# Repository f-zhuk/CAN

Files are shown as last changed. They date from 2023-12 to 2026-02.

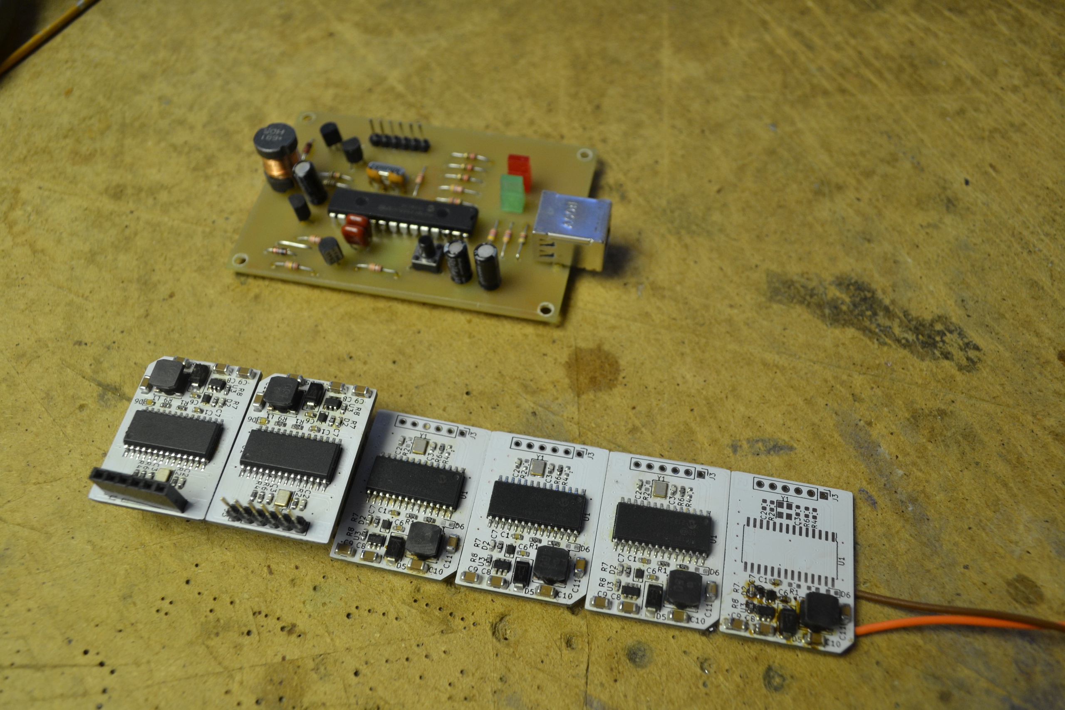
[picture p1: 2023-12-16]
CANMCU/Assemble.jpg

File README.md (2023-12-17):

# CAN
## General description
The work is in progress and is currently not ready for real-life application.  
This repository contains hardware, firmware, and software dedicated to the creation of custom CANopen systems for vehicles.  
Such custom systems could fit old cars with heavily damaged harnesses and vehicles that do not have electronic equipment by default, for example, boats, kayaks, and bicycles.
## Hardware
The complete system should consist of multiple functional blocks. Blocks should be as cheap and simple as possible while implementing complete functions like combination switch assembly, left tail light assembly, and door controls.  
Each functional block should be designed around a unified MCU module and simple interconnection boards to adapt signals from the MCU module to the systems of the block.  
Interconnection boards may provide 24LC I2C EEPROM memory for identification and non-volatile parameter storage.  
### MCU
MCU module should be self-sufficient and electrically ready for insertion in the CAN bus system. To achieve this, the MCU module has a power supply converter and CAN driver aside from the controller.  
For the first prototype, the PIC18 family was selected. PIC18F83K26 has a built-in CAN periphery and a reasonable price.  
MCU module has +12V power input, +5V power input/output, CAN, UART, 8xGPIO(PC7:PC0)  
### USB-UART
Most important interconnection board. It provides a USB to UART bridge to provide a simple debug interface.  
USB-UART board is built with MCP2200. It is connected not only through UART but also 5xGPIO. Additionally, 24LC16 I2C EEPROM memory is connected to C6 and C7. C5 is connected to the bus termination control.  
## Firmware
Heavily updated code described in AN945. The application note code was written for an older MCU. PIC18F83K26AN945 is not supported by the compiler the code was written for and the code is not compatible with the new compiler.  
AN945 default config:  
ADC is on (probably unused)  
PORT D is all output (probably unused)  
PORT B pin 5 is bit 0 of TPDO1, pin 4 is bit 1  
State of PORTB pins 4 and 5 compared to their states on previous DemoProcessEvents() call, change, rise and fall events detected and distinguished, written to OD  
Dictionary object 0x6005subondex 1 (uIOinIntEnable) bits 0 and 1  
Async transmission for TPDO1 by default  
PDO transmission type could be changed by writing to TPDO1 subindex 2  
## Software
The software is written in Python.

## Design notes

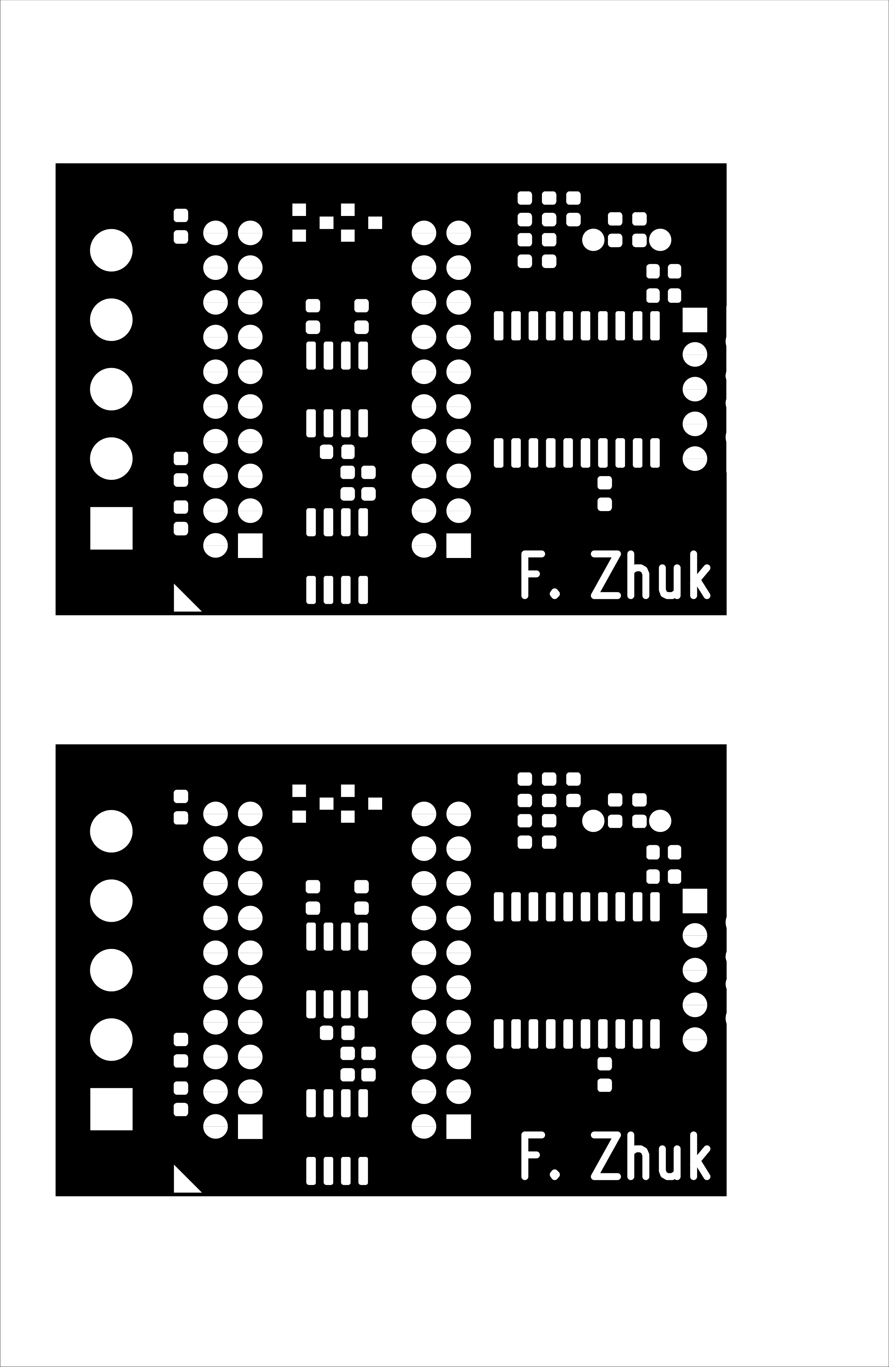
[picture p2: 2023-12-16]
USB-UART/B_Mask.png

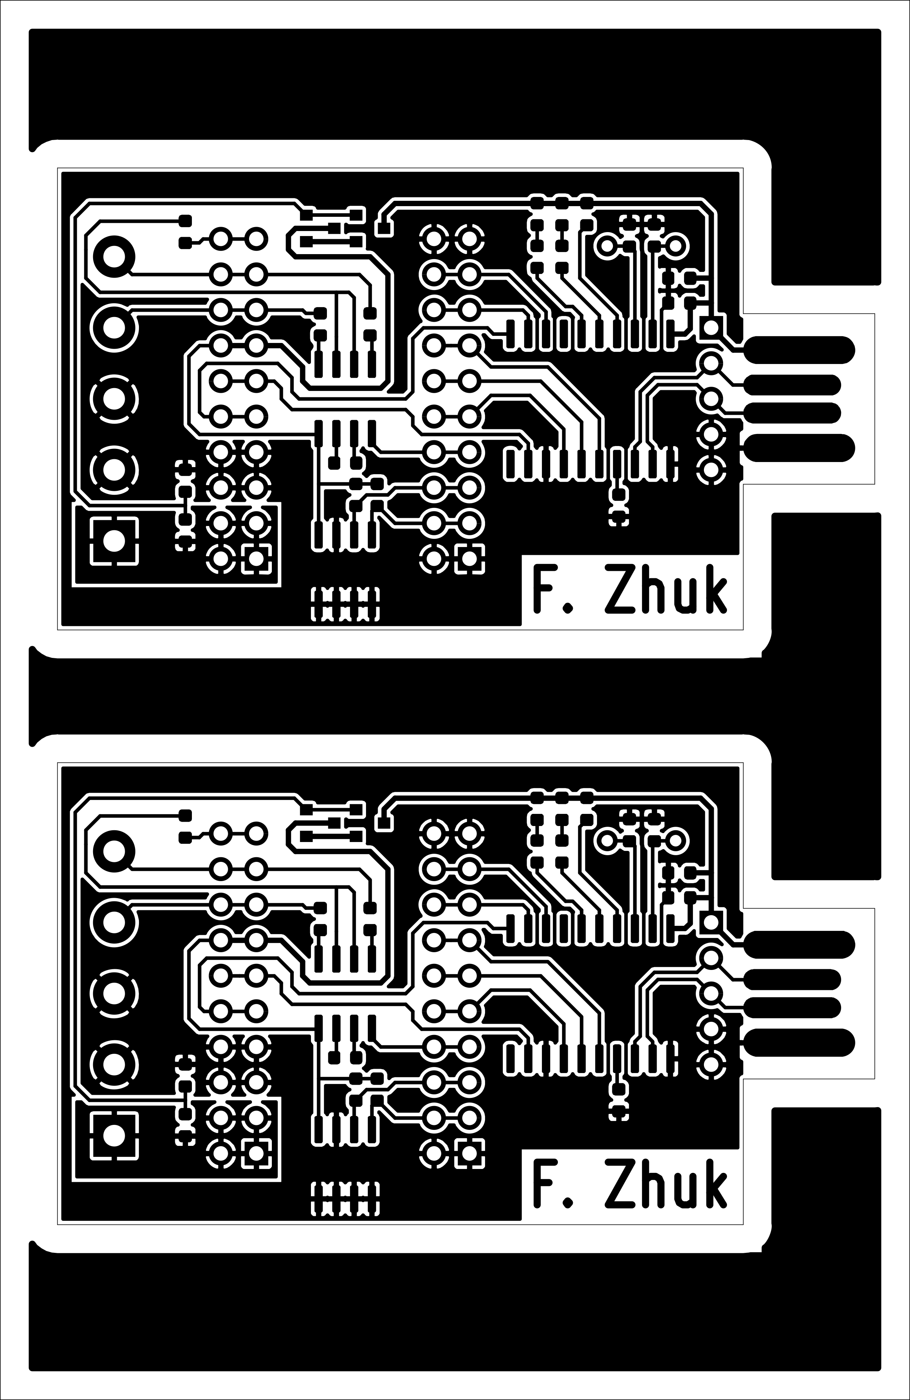
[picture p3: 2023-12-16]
USB-UART/B_Cu.png

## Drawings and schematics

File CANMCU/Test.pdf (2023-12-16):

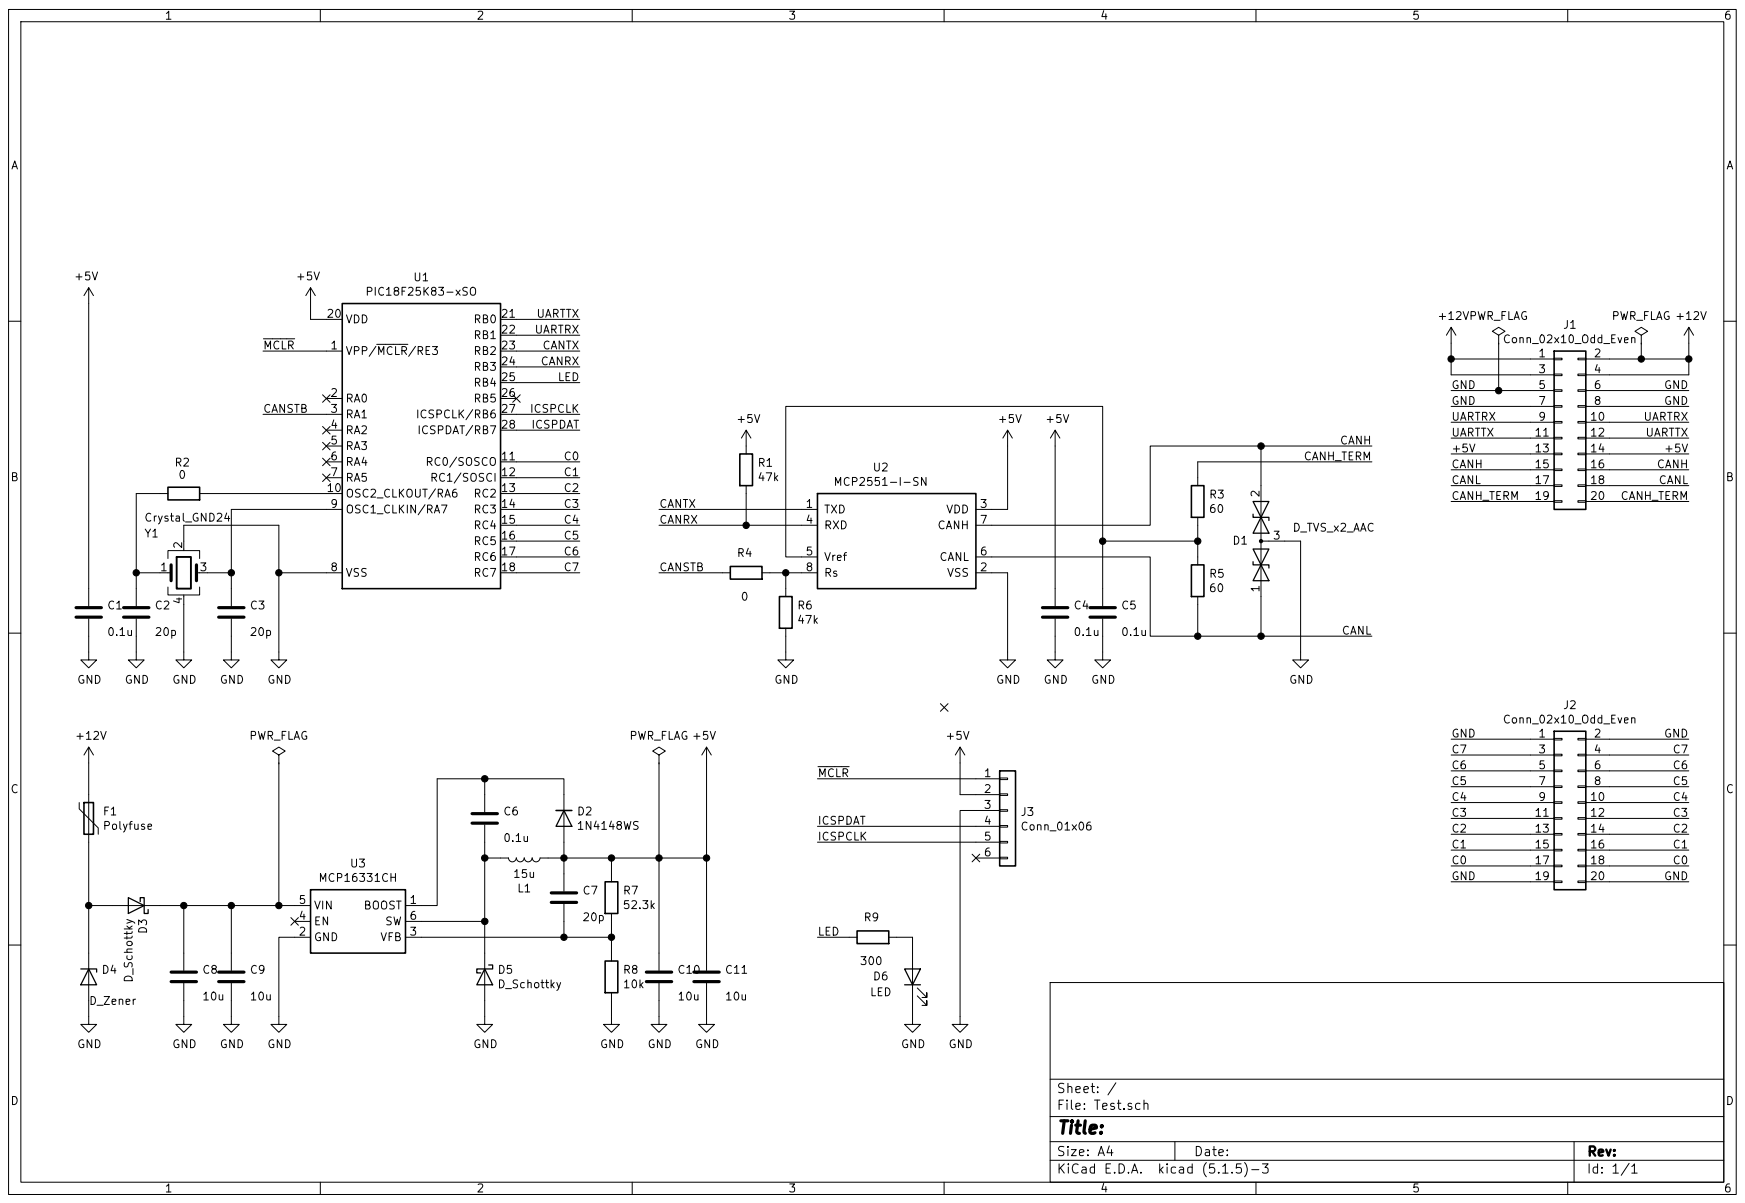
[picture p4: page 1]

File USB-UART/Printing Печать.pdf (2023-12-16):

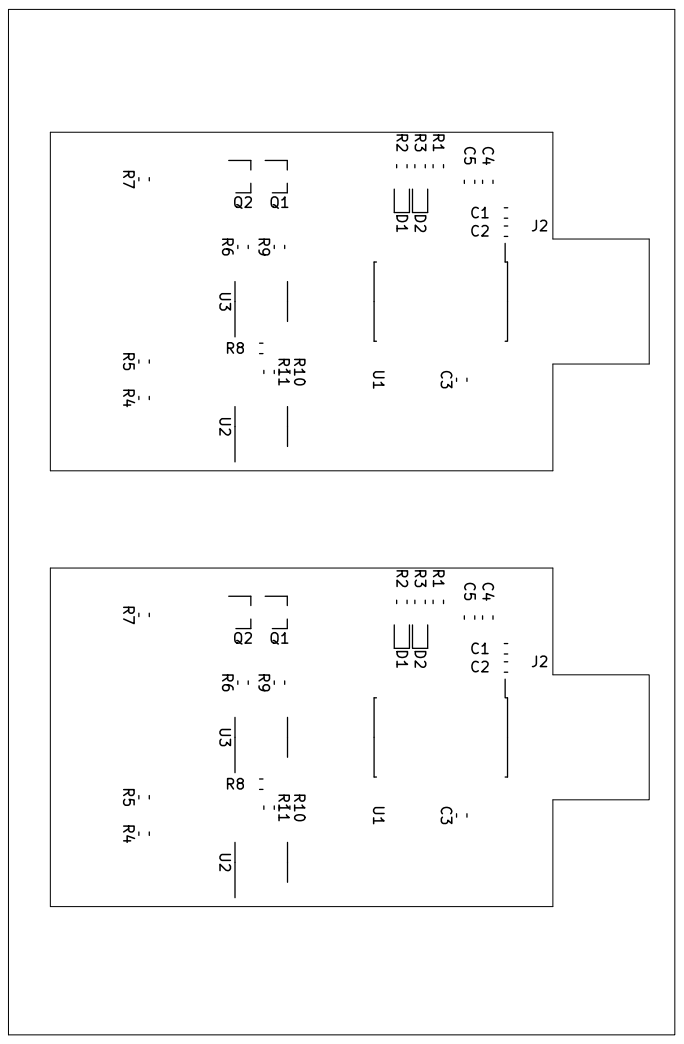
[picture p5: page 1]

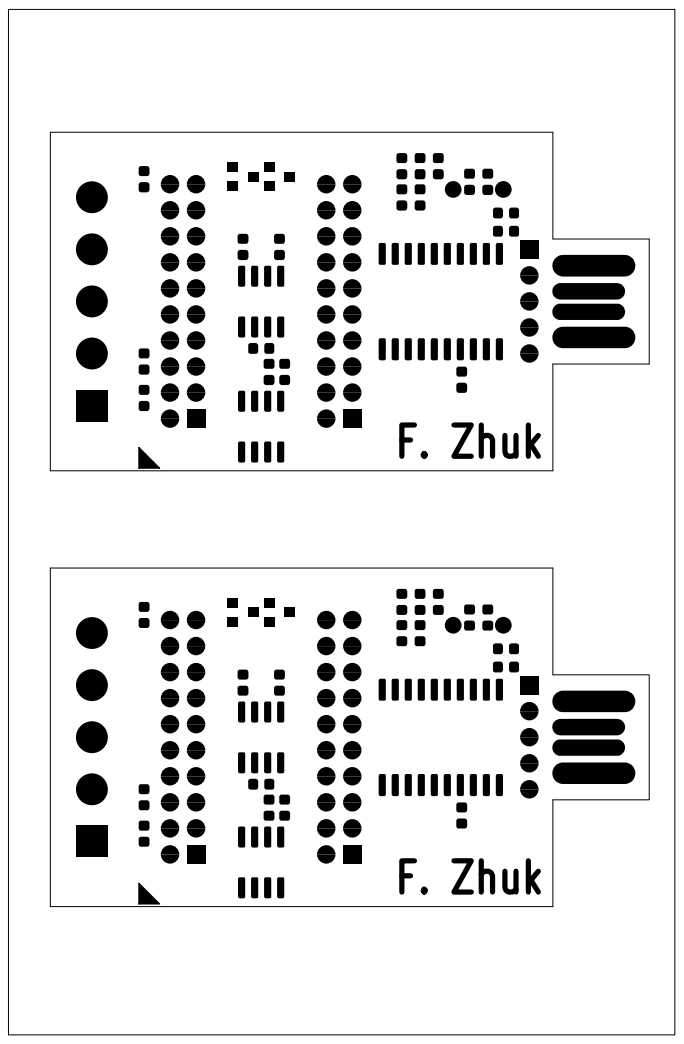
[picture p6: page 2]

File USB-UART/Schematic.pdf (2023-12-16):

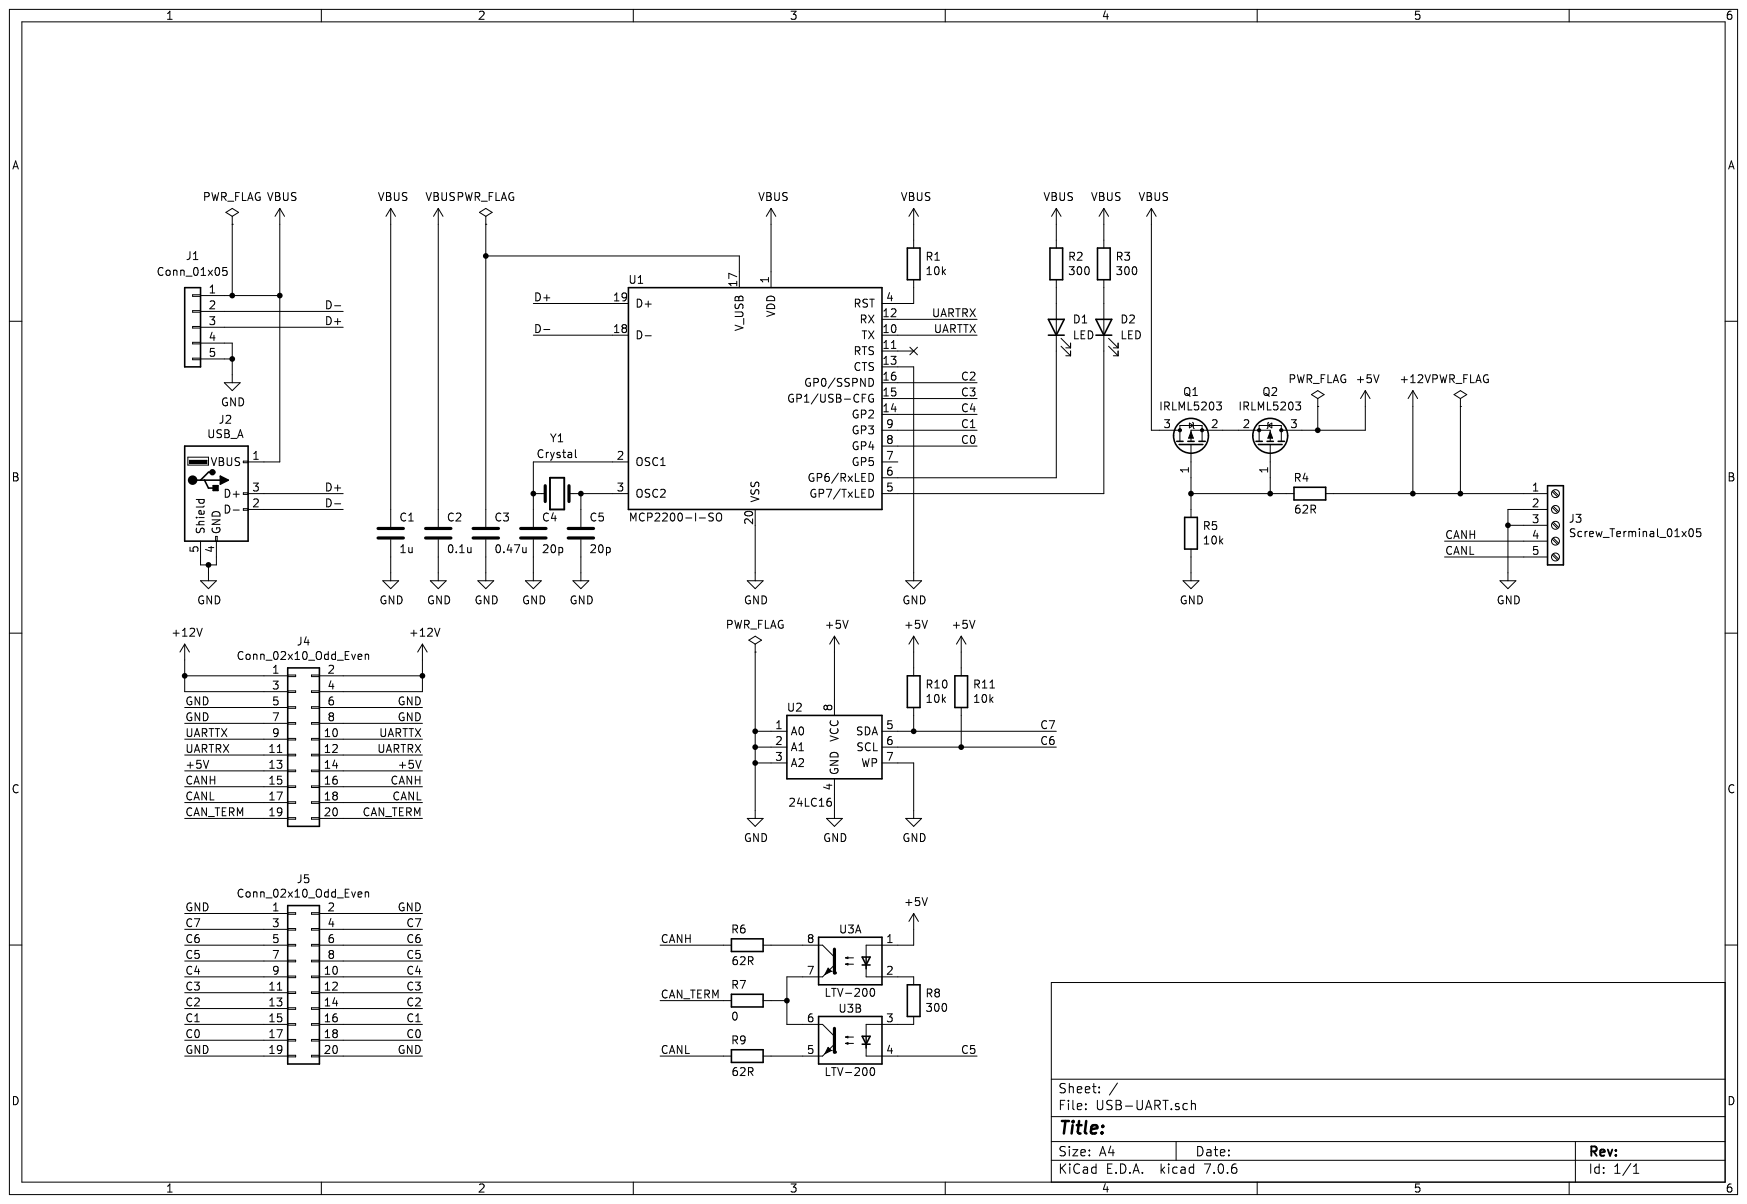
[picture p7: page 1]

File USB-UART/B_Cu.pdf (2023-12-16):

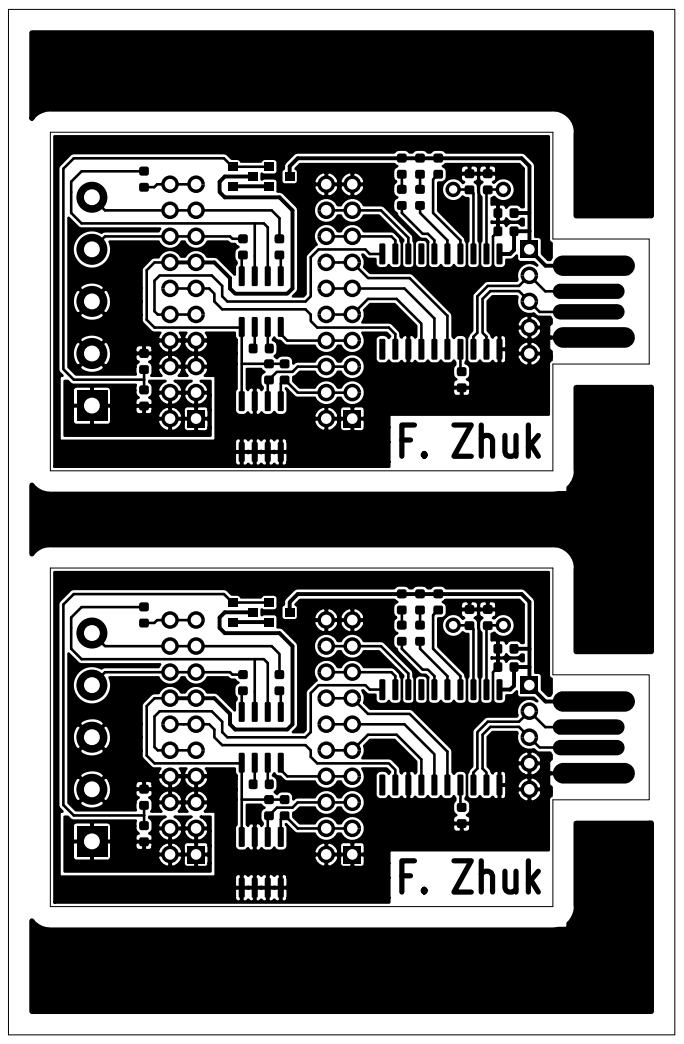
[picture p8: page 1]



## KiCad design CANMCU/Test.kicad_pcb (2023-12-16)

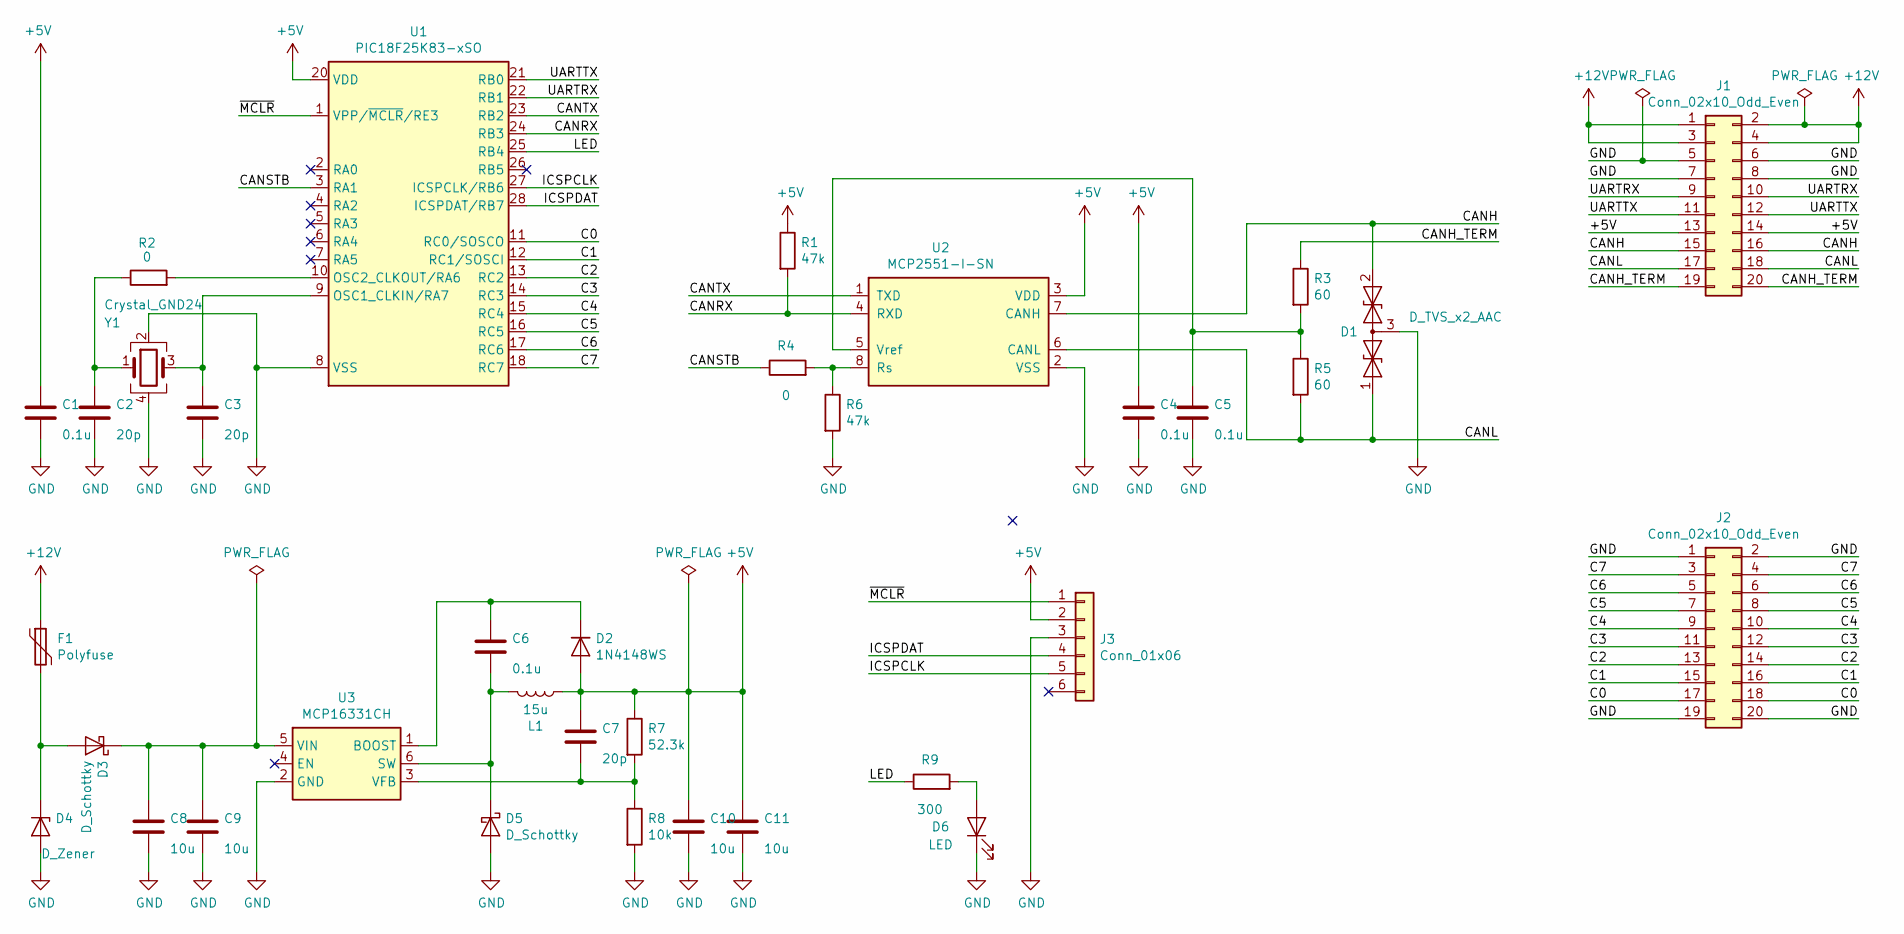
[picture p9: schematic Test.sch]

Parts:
C1, C4, C5, C6: 0.1u; C_0603_1608Metric
C2, C3, C7: 20p; C_0603_1608Metric
C8, C9, C10, C11: 10u; C_1206_3216Metric
D1: D_TVS_x2_AAC; SOT-23
D2: 1N4148WS; D_SOD-323
D3, D5: D_Schottky; D_SMA
D4: D_Zener; D_SMA
D6: LED; LED_0603_1608Metric
F1: Polyfuse; Fuse_1206_3216Metric
J1, J2: Conn_02x10_Odd_Even; PinHeader_2x10_P2.54mm_Vertical_SMD
J3: Conn_01x06; PinHeader_1x06_P2.54mm_Vertical
L1: 15u; L_Bourns_SRN6045TA
R1, R6: 47k; R_0603_1608Metric
R2, R4: 0; R_0603_1608Metric
R3, R5: 60; R_0603_1608Metric
R7: 52.3k; R_0603_1608Metric
R8: 10k; R_0603_1608Metric
R9: 300; R_0603_1608Metric
U1: PIC18F25K83-xSO; SOIC-28W_7.5x17.9mm_P1.27mm
U2: MCP2551-I-SN; SOIC-8_3.9x4.9mm_P1.27mm
U3: MCP16331CH; SOT-23-6
Y1: Crystal_GND24; Crystal_SMD_3225-4Pin_3.2x2.5mm

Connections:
+5V: C1.1, C4.1, C7.1, C10.1, C11.1, D2.2 (A), J1.13, J1.14, J3.2, L1.1, R1.1, R7.1, U1.20 (VDD), U2.3 (VDD)
+12V: F1.1, J1.1, J1.2, J1.3, J1.4
/C0: J2.17, J2.18, U1.11 (RC0/SOSCO)
/C1: J2.15, J2.16, U1.12 (RC1/SOSCI)
/C2: J2.13, J2.14, U1.13 (RC2)
/C3: J2.11, J2.12, U1.14 (RC3)
/C4: J2.9, J2.10, U1.15 (RC4)
/C5: J2.7, J2.8, U1.16 (RC5)
/C6: J2.5, J2.6, U1.17 (RC6)
/C7: J2.3, J2.4, U1.18 (RC7)
/CANH: D1.2 (A2), J1.15, J1.16, U2.7 (CANH)
/CANH_TERM: J1.19, J1.20, R3.1
/CANL: D1.1 (A1), J1.17, J1.18, R5.2, U2.6 (CANL)
/CANRX: R1.2, U1.24 (RB3), U2.4 (RXD)
/CANSTB: R4.1, U1.3 (RA1)
/CANTX: U1.23 (RB2), U2.1 (TXD)
/ICSPCLK: J3.5, U1.27 (ICSPCLK/RB6)
/ICSPDAT: J3.4, U1.28 (ICSPDAT/RB7)
/LED: R9.1, U1.25 (RB4)
/UARTRX: J1.9, J1.10, U1.22 (RB1)
/UARTTX: J1.11, J1.12, U1.21 (RB0)
/~MCLR: J3.1, U1.1 (VPP/~MCLR~/RE3)
GND: C1.2, C2.2, C3.2, C4.2, C5.2, C8.2, C9.2, C10.2, C11.2, D1.3 (common), D4.2 (A), D5.2 (A), D6.1 (K), J1.5, J1.6, J1.7, J1.8, J2.1, J2.2, J2.19, J2.20, J3.3, R6.2, R8.2, U1.8 (VSS), U1.19 (VSS), U2.2 (VSS), U3.2 (GND), Y1.2, Y1.4
unnamed: C2.1, R2.1, Y1.1
unnamed: C3.1, U1.9 (OSC1_CLKIN/RA7), Y1.3
unnamed: C5.1, R3.2, R5.1, U2.5 (Vref)
unnamed: C6.1, D2.1 (K), U3.1 (BOOST)
unnamed: C6.2, D5.1 (K), L1.2, U3.6 (SW)
unnamed: C7.2, R7.2, R8.1, U3.3 (VFB)
unnamed: C8.1, C9.1, D3.1 (K), U3.5 (VIN)
unnamed: D3.2 (A), D4.1 (K), F1.2
unnamed: D6.2 (A), R9.2
unnamed: R2.2, U1.10 (OSC2_CLKOUT/RA6)
unnamed: R4.2, R6.1, U2.8 (Rs)

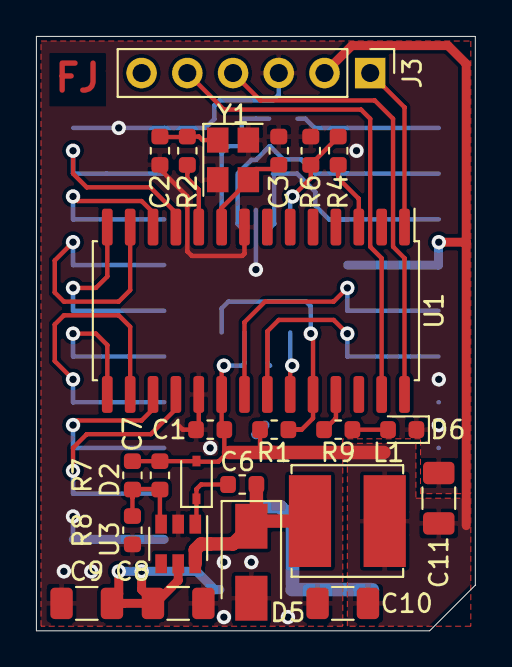
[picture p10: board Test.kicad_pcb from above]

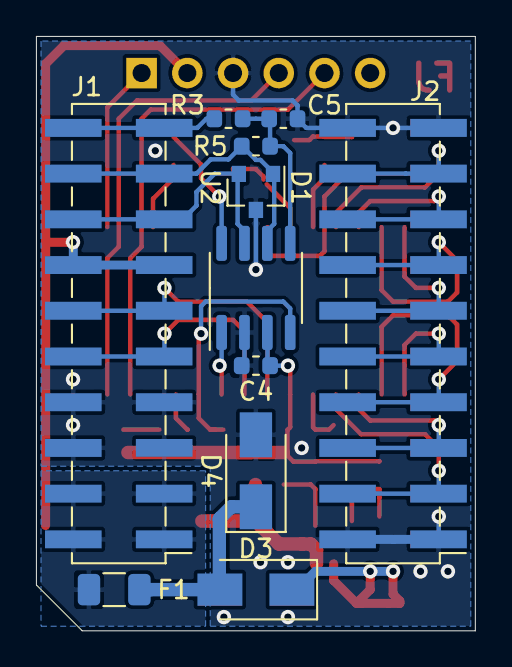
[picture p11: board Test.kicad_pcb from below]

Board: 4 copper layers, 24.4 x 33.0 mm, 35 parts (11 on the bottom side), 34 nets.

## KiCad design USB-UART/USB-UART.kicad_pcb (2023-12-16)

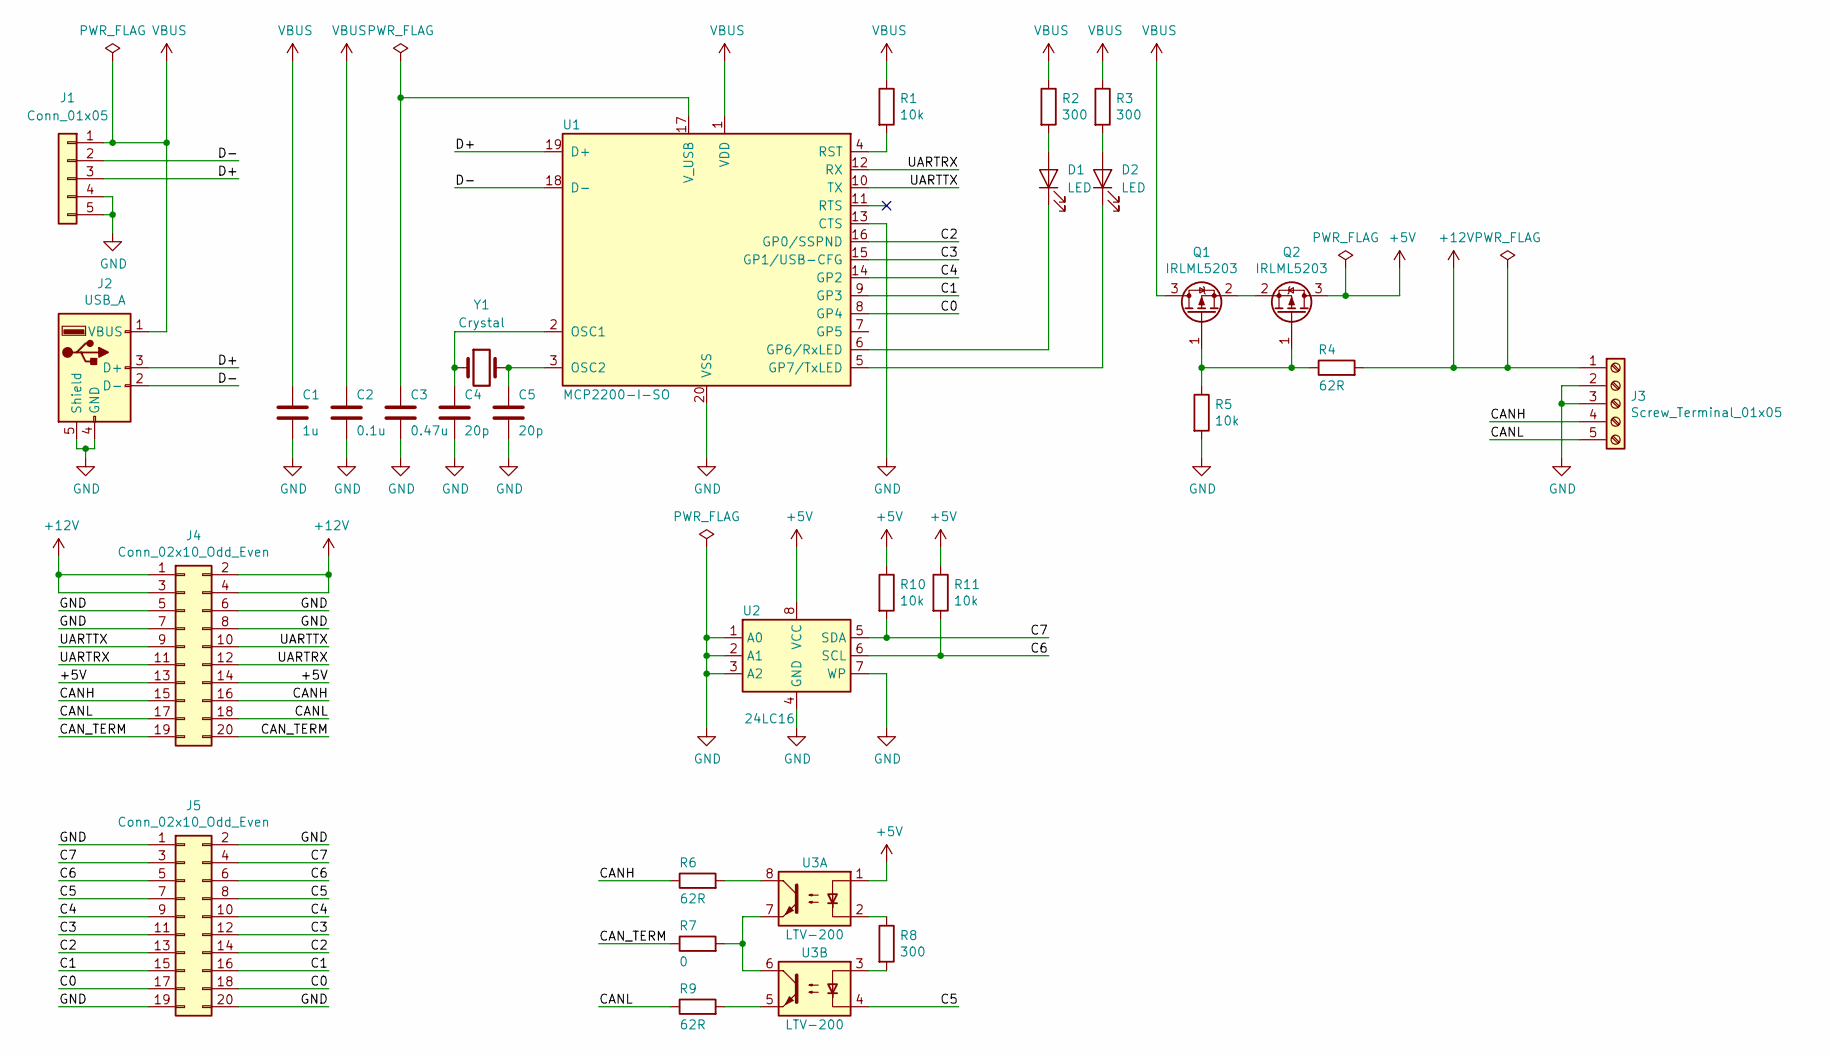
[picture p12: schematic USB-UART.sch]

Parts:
C1: 1u; C_0603_1608Metric
C2: 0.1u; C_0603_1608Metric
C3: 0.47u; C_0603_1608Metric
C4, C5: 20p; C_0603_1608Metric
D1, D2: LED; LED_0603_1608Metric
J1: Conn_01x05; PinHeader_1x05_P2.54mm_Vertical
J2: USB_A; USB_A_Integrated
J3: Screw_Terminal_01x05; TerminalBlock_bornier-5_P5.08mm
J4, J5: Conn_02x10_Odd_Even; PinSocket_2x10_P2.54mm_Vertical
Q1, Q2: IRLML5203; SOT-23
R1, R5, R10, R11: 10k; R_0603_1608Metric
R2, R3, R8: 300; R_0603_1608Metric
R4, R6, R9: 62R; R_0603_1608Metric
R7: 0; R_0603_1608Metric
U1: MCP2200-I-SO; SOIC-20W_7.5x12.8mm_P1.27mm
U2: 24LC16; SOIC-8_3.9x4.9mm_P1.27mm
U3: LTV-200; SOIC-8_3.9x4.9mm_P1.27mm
Y1: Crystal; Crystal_HC49-U_Vertical

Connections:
+5V: J4.13, J4.14, Q2.3 (D), R10.1, R11.1, U2.8 (VCC), U3.1
+12V: J3.1, J4.1, J4.2, J4.3, J4.4, R4.2
/C0: J5.17, J5.18, U1.8 (GP4)
/C1: J5.15, J5.16, U1.9 (GP3)
/C2: J5.13, J5.14, U1.16 (GP0/SSPND)
/C3: J5.11, J5.12, U1.15 (GP1/USB-CFG)
/C4: J5.9, J5.10, U1.14 (GP2)
/C5: J5.7, J5.8, U3.4
/C6: J5.5, J5.6, R11.2, U2.6 (SCL)
/C7: J5.3, J5.4, R10.2, U2.5 (SDA)
/CANH: J3.4, J4.15, J4.16, R6.1
/CANL: J3.5, J4.17, J4.18, R9.1
/CAN_TERM: J4.19, J4.20, R7.1
/D+: J1.3, J2.3 (D+), U1.19 (D+)
/D-: J1.2, J2.2 (D-), U1.18 (D-)
/UARTRX: J4.11, J4.12, U1.12 (RX)
/UARTTX: J4.9, J4.10, U1.10 (TX)
GND: C1.2, C2.2, C3.2, C4.2, C5.2, J1.4, J1.5, J2.4 (GND), J2.5 (Shield), J3.2, J3.3, J4.5, J4.6, J4.7, J4.8, J5.1, J5.2, J5.19, J5.20, R5.2, U1.13 (CTS), U1.20 (VSS), U2.1 (A0), U2.2 (A1), U2.3 (A2), U2.4 (GND), U2.7 (WP)
unnamed: C3.1, U1.17 (V_USB)
unnamed: C4.1, U1.2 (OSC1), Y1.1
unnamed: C5.1, U1.3 (OSC2), Y1.2
unnamed: D1.1 (K), U1.6 (GP6/RxLED)
unnamed: D1.2 (A), R2.2
unnamed: D2.1 (K), U1.5 (GP7/TxLED)
unnamed: D2.2 (A), R3.2
unnamed: Q1.1 (G), Q2.1 (G), R4.1, R5.1
unnamed: Q1.2 (S), Q2.2 (S)
unnamed: R1.2, U1.4 (RST)
unnamed: R6.2, U3.8
unnamed: R7.2, U3.6, U3.7
unnamed: R8.1, U3.2
unnamed: R8.2, U3.3
unnamed: R9.2, U3.5
VBUS: C1.1, C2.1, J1.1, J2.1 (VBUS), Q1.3 (D), R1.1, R2.1, R3.1, U1.1 (VDD)

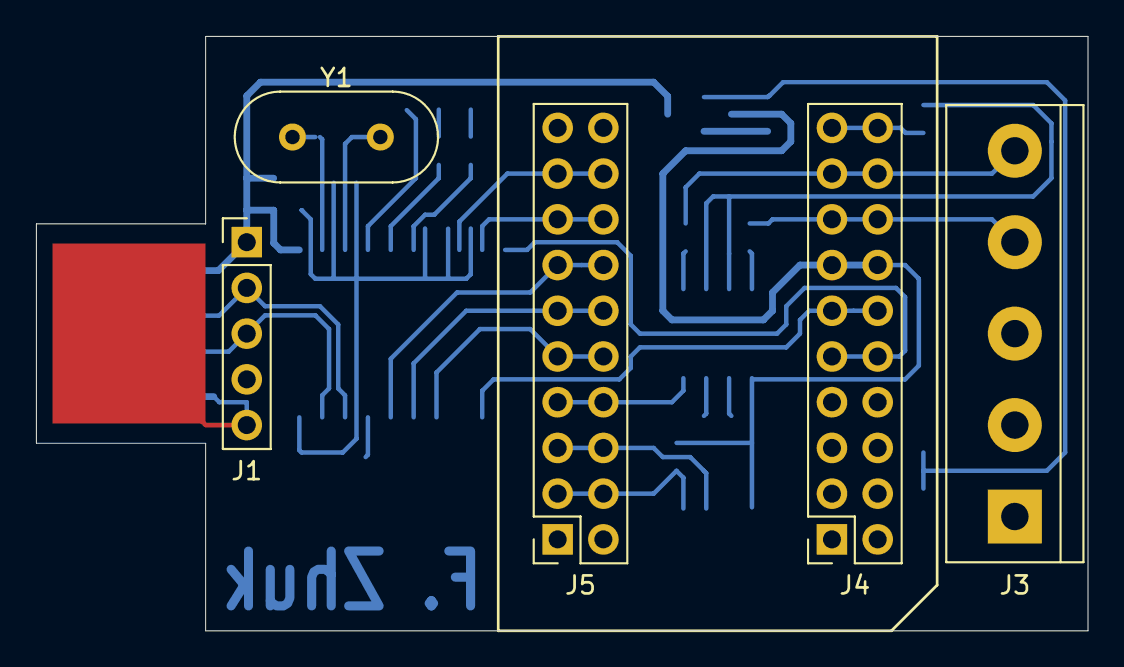
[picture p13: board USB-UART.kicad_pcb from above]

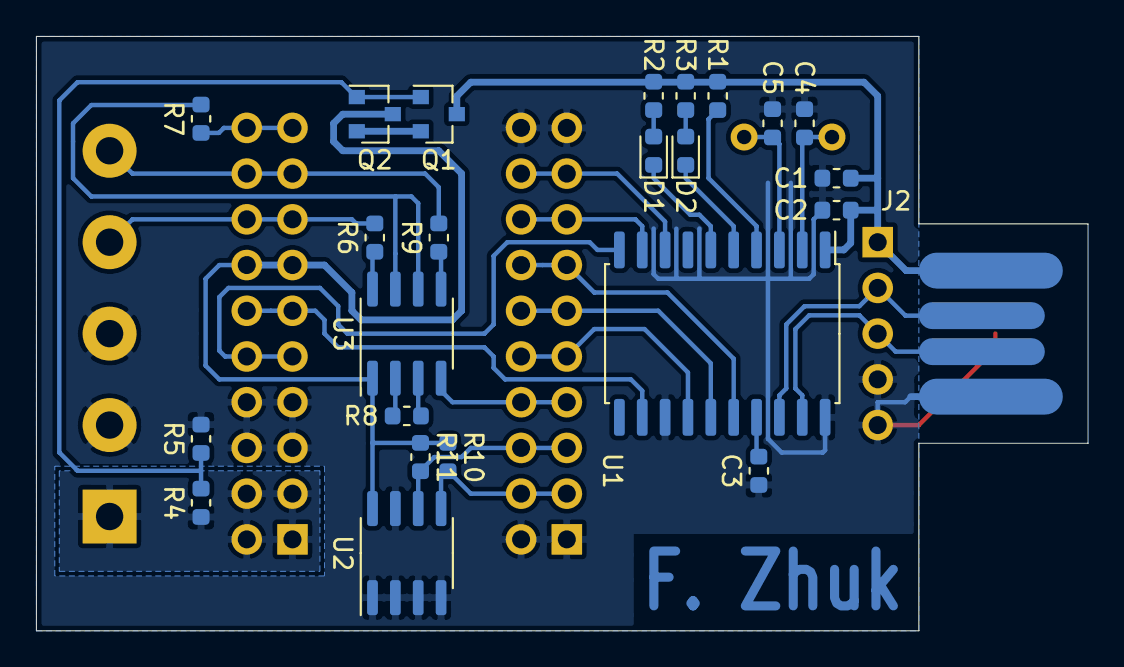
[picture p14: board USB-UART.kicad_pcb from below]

Board: 2 copper layers, 58.4 x 33.0 mm, 29 parts (24 on the bottom side), 34 nets.

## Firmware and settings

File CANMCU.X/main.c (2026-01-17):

/**
  Generated Main Source File

  Company:
    Microchip Technology Inc.

  File Name:
    main.c

  Summary:
    This is the main file generated using PIC10 / PIC12 / PIC16 / PIC18 MCUs

  Description:
    This header file provides implementations for driver APIs for all modules selected in the GUI.
    Generation Information :
        Product Revision  :  PIC10 / PIC12 / PIC16 / PIC18 MCUs - 1.81.7
        Device            :  PIC18F26K83
        Driver Version    :  2.00
*/

/*
    (c) 2018 Microchip Technology Inc. and its subsidiaries. 
    
    Subject to your compliance with these terms, you may use Microchip software and any 
    derivatives exclusively with Microchip products. It is your responsibility to comply with third party 
    license terms applicable to your use of third party software (including open source software) that 
    may accompany Microchip software.
    
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
    IN NO EVENT WILL MICROCHIP BE LIABLE FOR ANY INDIRECT, SPECIAL, PUNITIVE, 
    INCIDENTAL OR CONSEQUENTIAL LOSS, DAMAGE, COST OR EXPENSE OF ANY KIND 
    WHATSOEVER RELATED TO THE SOFTWARE, HOWEVER CAUSED, EVEN IF MICROCHIP 
    HAS BEEN ADVISED OF THE POSSIBILITY OR THE DAMAGES ARE FORESEEABLE. TO 
    THE FULLEST EXTENT ALLOWED BY LAW, MICROCHIP'S TOTAL LIABILITY ON ALL 
    CLAIMS IN ANY WAY RELATED TO THIS SOFTWARE WILL NOT EXCEED THE AMOUNT 
    OF FEES, IF ANY, THAT YOU HAVE PAID DIRECTLY TO MICROCHIP FOR THIS 
    SOFTWARE.
*/

#include "CANopen/CO_MAIN.h"
#include "main.h"
//#include "CANopen/CO_PDO1.h"
//#include "CANopen/Timer.h"
#include "mcc_generated_files/mcc.h"


#define	RTR_DIS	bytes.B1.bits.b2
#define STD_DIS	bytes.B1.bits.b3
#define PDO_DIS	bytes.B1.bits.b4

// These are mapping constants for TPDO1 
// starting at 0x1A00 in the dictionary
const unsigned long uTPDO1Map = 0x60000108; // 0x1A00 subindex 1 in CO_PDO.def 
const unsigned long uRPDO1Map = 0x62000108; // 0x1600 subindex 1 in CO_PDO.def 
const unsigned long uPDO1Dummy = 0x00000008;

unsigned char uIOinFilter;					// 0x6003 filter
unsigned char uIOinPolarity;				// 0x6002 polarity
unsigned char uIOinIntChange;				// 0x6006 interrupt on change
unsigned char uIOinIntRise;					// 0x6007 interrupt on positive edge
unsigned char uIOinIntFall;					// 0x6008 interrupt on negative edge
unsigned char uIOinIntEnable;				// 0x6005 enable interrupts

unsigned char uIOinDigiInOld;				// 

// Static data refered to by the dictionary
const unsigned char rMaxIndex1 = 1;
const unsigned char rMaxIndex2 = 8;
const unsigned char uDemoTPDO1Len = 2;


unsigned char uLocalXmtBuffer[8];			// Local buffer for TPDO1
unsigned char uLocalRcvBuffer[8];			// local buffer fot RPDO1

UNSIGNED8 uDemoState; 					// Bits used to control various states
unsigned char uDemoSyncCount;			// Counter for synchronous types
unsigned char uDemoSyncSet;				// Internal TPDO type control


/*********************************************************************
 * Function:        void DemoInit(void)
 *
 * PreCondition:    none
 *
 * Input:       	none
 *                  
 * Output:         	none  
 *
 * Side Effects:    none
 *
 * Overview:        This is the initialization to the demonstration
 *					object.
 *
 * Note:          	
 ********************************************************************/
void DemoInit(void)
{
	uDemoSyncSet = 255;

	uIOinFilter = 0;
	uIOinPolarity = 0;
	uIOinIntChange = 1;
	uIOinIntRise = 0;
	uIOinIntFall = 0;
	uIOinIntEnable = 1;

	uIOinDigiInOld = uLocalXmtBuffer[0] = 0;
	uLocalRcvBuffer[1] = uLocalXmtBuffer[1] = 0;
	uLocalRcvBuffer[2] = uLocalXmtBuffer[2] = 0;
	uLocalRcvBuffer[3] = uLocalXmtBuffer[3] = 0;
	uLocalRcvBuffer[4] = uLocalXmtBuffer[4] = 0;
	uLocalRcvBuffer[5] = uLocalXmtBuffer[5] = 0;
	uLocalRcvBuffer[6] = uLocalXmtBuffer[6] = 0;
	uLocalRcvBuffer[7] = uLocalXmtBuffer[7] = 0;


	// Convert to MCHP
	mTOOLS_CO2MCHP(mCOMM_GetNodeID().byte + 0xC0000180L);
	
	// Store the COB
	mTPDOSetCOB(1, mTOOLS_GetCOBID());

	// Convert to MCHP
	mTOOLS_CO2MCHP(mCOMM_GetNodeID().byte + 0xC0000200L);
	
	// Store the COB
	mRPDOSetCOB(1, mTOOLS_GetCOBID());
	
	// Set the pointer to the buffers
	mTPDOSetTxPtr(1, (unsigned char *)(&uLocalXmtBuffer[0]));
	//_uPDO1.TPDO.buf = (unsigned char *)(&uLocalXmtBuffer[0]);

	// Set the pointer to the buffers
	mRPDOSetRxPtr(1, (unsigned char *)(&uLocalRcvBuffer[0]));
    //_uPDO1.RPDO.buf = (unsigned char *)(&uLocalRcvBuffer[0]));

	// Set the length
	mTPDOSetLen(1, 8);
    //_uPDO1.TPDO.len = 8
}

/*********************************************************************
 * Function:        void CO_COMMSyncEvent(void)
 *
 * PreCondition:    none
 *
 * Input:       	none
 *                  
 * Output:         	none  
 *
 * Side Effects:    none
 *
 * Overview:        This is a simple demonstration of a SYNC event 
 *					handling function.
 *
 * Note:          	
 ********************************************************************/
void CO_COMMSyncEvent(void)
{
	// Process only if in a synchronous mode
	if ((uDemoSyncSet == 0) && (uDemoState.bits.b2))
	{
		// Reset the synchronous transmit and transfer to async
		uDemoState.bits.b2 = 0;
		uDemoState.bits.b0 = 1;
	}
	else
	if ((uDemoSyncSet >= 1) && (uDemoSyncSet <= 240))
	{
		// Adjust the sync counter
		uDemoSyncCount--;
		
		// If time to generate sync
		if (uDemoSyncCount == 0)
		{
			// Reset the sync counter
			uDemoSyncCount = uDemoSyncSet;
			
			// Start the PDO transmission
			uDemoState.bits.b0 = 1;
		}
	}
}

/*********************************************************************
 * Function:        void DemoProcessEvents(void)
 *
 * PreCondition:    none
 *
 * Input:       	none
 *                  
 * Output:         	none  
 *
 * Side Effects:    none
 *
 * Overview:        This is a simple demonstration of a demo state
 *					machine for cooperative multitasking.
 *
 * Note:          	
 ********************************************************************/
void DemoProcessEvents(void)
{
	//unsigned char change;
	//unsigned char rise;
	//unsigned char fall;

	// Read the input port
	//(*(UNSIGNED8 *)uLocalXmtBuffer).bits.b0 = PORTBbits.RB5;					
	//(*(UNSIGNED8 *)uLocalXmtBuffer).bits.b1 = PORTBbits.RB4;					
	

	// Determine the change if any
	//change = uIOinDigiInOld ^ uLocalXmtBuffer[0];
	
	// Determine if there were any rise events
	//rise = (uIOinIntRise & change) & uLocalXmtBuffer[0];
		
	// Determine if there were any fall events
	//fall = (uIOinIntFall & change) & ~uLocalXmtBuffer[0];

	// Determine if there were any change events
	//change = (uIOinIntChange & change);

	// Cycle the current value to the old
	//uIOinDigiInOld = uLocalXmtBuffer[0];

	// If any of these are true then indicate an interrupt condition
	//if (uIOinIntEnable & (change | rise | fall)) uDemoState.bits.b1 = 1;

	//if (uDemoState.bits.b1)
	//{
	//	switch (uDemoSyncSet)
	//	{
	//		case 0:				// Asyclic synchronous transmit
	//			// Set a synchronous transmit flag
	//			uDemoState.bits.b2 = 1;
	//			break;

	//		case 254:			// Asynchronous transmit
	//		case 255:						
				// Reset the asynchronous transmit flag
	//			uDemoState.bits.b0 = 1;
	//			break;
	//	}
	//}

    (*(UNSIGNED8 *)uLocalXmtBuffer).byte ++;
	// If ready to send 
	if (mTPDOIsPutRdy(1))// && uDemoState.bits.b0)
	{
		// Tell the stack data is loaded for transmit
		mTPDOWritten(1);
		
		// Reset any synchronous or asynchronous flags
		//uDemoState.bits.b0 = 0;
		//uDemoState.bits.b1 = 0;
	}

	// If any data has been received
	//if (mRPDOIsGetRdy(1))
	//{
		// Write out the first byte of the buffer
	//	LATB = uLocalRcvBuffer[0];
		
		// PDO read, free the driver to accept more data
	//	mRPDORead(1);
	//}
}

/*********************************************************************
 * Function:        void CO_COMM_RPDO1_COBIDAccessEvent(void)
 *
 * PreCondition:    none
 *
 * Input:       	none
 *                  
 * Output:         	none  
 *
 * Side Effects:    none
 *
 * Overview:        This is a simple demonstration of a RPDO COB access
 *					handling function.
 *
 * Note:          	This function is called from the dictionary.
 ********************************************************************/
void CO_COMM_RPDO1_COBIDAccessEvent(void)
{
	switch (mCO_DictGetCmd())
	{
        case DICT_OBJ_INFO:		// Get information not required for this object
			break;
          
		case DICT_OBJ_READ: 	// Read the object
			// Translate MCHP COB to CANopen COB
			//mTOOLS_MCHP2CO(mRPDOGetCOB(1));
            mTOOLS_MCHP2CO(uRPDOComm1.word);
			
			// Return the COBID
			*(unsigned long *)(uDict.obj->pReqBuf) = mTOOLS_GetCOBID();
			break;

		case DICT_OBJ_WRITE: 	// Write the object
			// Translate the COB to MCHP format
			mTOOLS_CO2MCHP(*(unsigned long *)(uDict.obj->pReqBuf));
			
			// If the request is to stop the PDO
			if ((*(UNSIGNED32 *)(&mTOOLS_GetCOBID())).PDO_DIS)
			{
				// And if the COB received matches the stored COB and type then close
				//if (!((mTOOLS_GetCOBID() ^ mRPDOGetCOB(1)) & 0xFFFFEFFFL))
                if (!((mTOOLS_GetCOBID() ^ uRPDOComm1.word) & 0xFFFFEFFFL))    
				{
					// but only close if the PDO endpoint was open
					if (mRPDOIsOpen(1)) {mRPDOClose(1);}
		
					// Indicate to the local object that this PDO is disabled
					//(*(UNSIGNED32 *)(&mRPDOGetCOB(1))).PDO_DIS = 1;
                    (*(UNSIGNED32 *)(&uRPDOComm1.word)).PDO_DIS = 1;
				}
				else {mCO_DictSetRet(E_PARAM_RANGE);} //error
			}

			// Else if the TPDO is not open then start the TPDO
			else
			{
				// And if the COB received matches the stored COB and type then open
				if (!((mTOOLS_GetCOBID() ^ mRPDOGetCOB(1)) & 0xFFFFEFFFL))
				{
					// but only open if the PDO endpoint was closed
					if (!mRPDOIsOpen(1)) {mRPDOOpen(1);}
						
					// Indicate to the local object that this PDO is enabled
					(*(UNSIGNED32 *)(&mRPDOGetCOB(1))).PDO_DIS = 0;
				}
				else {mCO_DictSetRet(E_PARAM_RANGE);} //error
			}
			break;
	}	
}

/*********************************************************************
 * Function:        void CO_COMM_TPDO1_COBIDAccessEvent(void)
 *
 * PreCondition:    none
 *
 * Input:       	none
 *                  
 * Output:         	none  
 *
 * Side Effects:    none
 *
 * Overview:        This is a simple demonstration of a TPDO COB access
 *					handling function.
 *
 * Note:          	This function is called from the dictionary.
 ********************************************************************/
void CO_COMM_TPDO1_COBIDAccessEvent(void)
{
	switch (mCO_DictGetCmd())
	{
		case DICT_OBJ_INFO:		// Get information not required for this object
			break;
            
        case DICT_OBJ_READ: 	// Read the object
			// Translate MCHP COB to CANopen COB
			mTOOLS_MCHP2CO(mTPDOGetCOB(1));
			
			// Return the COBID
			*(unsigned long *)(uDict.obj->pReqBuf) = mTOOLS_GetCOBID();
			break;

		case DICT_OBJ_WRITE: 	// Write the object
			// Translate the COB to MCHP format
			mTOOLS_CO2MCHP(*(unsigned long *)(uDict.obj->pReqBuf));
			
			// If the request is to stop the PDO
			if ((*(UNSIGNED32 *)(&mTOOLS_GetCOBID())).PDO_DIS)
			{
				// And if the COB received matches the stored COB and type then close
				if (!((mTOOLS_GetCOBID() ^ mTPDOGetCOB(1)) & 0xFFFFEFFFL))
				{
					// but only close if the PDO endpoint was open
					if (mTPDOIsOpen(1)) {mTPDOClose(1);}
		
					// Indicate to the local object that this PDO is disabled
					(*(UNSIGNED32 *)(&mTPDOGetCOB(1))).PDO_DIS = 1;
				}
				else {mCO_DictSetRet(E_PARAM_RANGE);} //error
			}

			// Else if the TPDO is not open then start the TPDO
			else
			{
				// And if the COB received matches the stored COB and type then open
				if (!((mTOOLS_GetCOBID() ^ mTPDOGetCOB(1)) & 0xFFFFEFFFL))
				{
					// but only open if the PDO endpoint was closed
					if (!mTPDOIsOpen(1)) {mTPDOOpen(1);}
						
					// Indicate to the local object that this PDO is enabled
					(*(UNSIGNED32 *)(&mTPDOGetCOB(1))).PDO_DIS = 0;
				}
				else {mCO_DictSetRet(E_PARAM_RANGE);} //error
			}
			break;
	}	
}

/*********************************************************************
 * Function:        void CO_COMM_TPDO1_TypeAccessEvent(void)
 *
 * PreCondition:    none
 *
 * Input:       	none
 *                  
 * Output:         	none  
 *
 * Side Effects:    none
 *
 * Overview:        This is a simple demonstration of a TPDO type access
 *					handling function.
 *
 * Note:          	This function is called from the dictionary.
 ********************************************************************/
void CO_COMM_TPDO1_TypeAccessEvent(void)
{
	unsigned char tempType;
	
	switch (mCO_DictGetCmd())
	{
		case DICT_OBJ_INFO:		// Get information about the object
			// The application should use this to load the 
			// structure with legth, access, and mapping.
			break;

		case DICT_OBJ_READ: 	// Read the object
			// Write the Type to the buffer
			*(uDict.obj->pReqBuf) = uDemoSyncSet;
			break;

		case DICT_OBJ_WRITE: 	// Write the object
			tempType = *(uDict.obj->pReqBuf);
			if ((tempType >= 0) && (tempType <= 240))
			{
				// Set the new type and resync
				uDemoSyncCount = uDemoSyncSet = tempType;
			}
			else 
			if ((tempType == 254) || (tempType == 255))
			{
				uDemoSyncSet = tempType;
			}
			else {mCO_DictSetRet(E_PARAM_RANGE);} //error
			
			break;
	}	
}

/*********************************************************************
 * Function:        void CO_PDO1LSTimerEvent(void)
 *
 * PreCondition:    none
 *
 * Input:       	none
 *                  
 * Output:         	none  
 *
 * Side Effects:    none
 *
 * Overview:        none
 *
 * Note:          	none
 ********************************************************************/
void CO_PDO1LSTimerEvent(void)
{
	
}



/*********************************************************************
 * Function:        void CO_PDO1TXFinEvent(void)
 *
 * PreCondition:    none
 *
 * Input:       	none
 *                  
 * Output:         	none  
 *
 * Side Effects:    none
 *
 * Overview:        none
 *
 * Note:          	none
 ********************************************************************/
void CO_PDO1TXFinEvent(void)
{
	
}

/*
                         Main application
 */
void TMR0_Blink(void){
    
    ////uCAN_MSG send;
    ////uint8_t i= 7;
 
    ////send.frame.id = 0xAA;
    ////send.frame.idType = dSTANDARD_CAN_MSG_ID_2_0B;
    ////send.frame.dlc = 1;
           
    ////send.array[0] = 0x55;
    
    ////CAN_transmit(&send);
    
    // add your TMR0 interrupt custom code
    // or set custom function using TMR0_SetInterruptHandler()
    //if(COMM_NETCTL_EN)
    //{
	// If ready to send 
    //*((UNSIGNED8 *)(mTPDOGetTxPtr(1))) = 0x04;
    //*((UNSIGNED8 *)(_uPDO1.TPDO.buf)) = 0x08;
	////if (mTPDOIsPutRdy(1))// && uDemoState.bits.b0)
	////{
        ////(*(UNSIGNED8 *)uLocalXmtBuffer).byte ++;
        ////(*(UNSIGNED8 *)uLocalXmtBuffer).bits.b0 = 1;
		// Tell the stack data is loaded for transmit
		////mTPDOWritten(1);
        //IO_RB4_Toggle();
		
		// Reset any synchronous or asynchronous flags
		//uDemoState.bits.b0 = 0;
		//uDemoState.bits.b1 = 0;
	////}
    //}
    //DemoProcessEvents();
    //IO_RB4_Toggle();
    //do { LATBbits.LATB4 = ~LATBbits.LATB4; } while(0);
    _CO_COMMLSTimeEventManager();
}

void UART1_Write_String(uint8_t *buffer_ptr)
{
    while(*buffer_ptr)
    {
        while(!UART1_is_tx_ready());
        UART1_Write(*buffer_ptr);
        buffer_ptr++;
    }
}

void main(void)
{
    
    // Initialize the device
    SYSTEM_Initialize();

    // If using interrupts in PIC18 High/Low Priority Mode you need to enable the Global High and Low Interrupts
    // If using interrupts in PIC Mid-Range Compatibility Mode you need to enable the Global Interrupts
    // Use the following macros to:

    // Enable the Global Interrupts
    INTERRUPT_GlobalInterruptEnable();

    // Disable the Global Interrupts
    //INTERRUPT_GlobalInterruptDisable();
    // Perform any application specific initialization
    //TimerInit(); // Init my timer
    TMR0_SetInterruptHandler(TMR0_Blink);
    TMR0_StartTimer();
    mSYNC_SetCOBID(0x1000); 		// Set the SYNC COB ID (MCHP format)
    mCO_SetNodeID(0x01); 		// Set the node_id
    mCO_SetBaud(0x05); 			// Set the baudrate 125kbit/s default
    mNMTE_SetHeartBeat(1000); 	// Set the initial heartbeat in ms
    mNMTE_SetGuardTime(0x00); 	// Set the initial guard time
    mNMTE_SetLifeFactor(0x00); 	// Set the initial life time
    DemoInit();
    _CO_COMMResetEventManager(); // mCO_InitAll(); Initialize CANopen to run/**/
    
    //mNMT_GotoOperState();
    
    while(1)
    {
    // Process CANopen events
        CO_ProcessAllEvents();
        //UART1_Write_String("Hello\r\n");
        //COMM_NETCTL_TF = 0;
        // Process application specific functions
        // 1ms timer events// Process application specific functions
		DemoProcessEvents();
        /*if (TimerIsOverflowEvent())
        {
        // Process timer related events
            mCO_ProcessAllTimeEvents();
        // Perform other time functions
        }*/
        //IO_RB4_Toggle();
        //__delay_ms(50);
    }
}
/**
 End of File
*/

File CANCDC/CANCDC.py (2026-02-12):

from datetime import datetime
from turtle import left
import os
import time
import serial
import serial.tools.list_ports
import tkinter as tk

#
#def port_search():
#    port_name = "none"
#    while port_name == "none":
#        for port in serial.tools.list_ports.comports():
#           if port.vid == 1240 and port.pid == 223:
#                port_name = port.name
#                return port_name
#        time.sleep(0.1)

#
window = tk.Tk()
window.title("CANCDC")
window.geometry('1000x600')
window.configure(background="white")
text = tk.StringVar()
text.set("No adapters presented")
greeting = tk.Label(window, bg="white", textvariable=text, font=("Montserrat Light", 20))
#greeting.place(relx = 0.5, rely = 0.5, anchor = 'center')

class CANFrame:
    def __init__(self, ID, DLC, DATA):
        self.__ID = ID
        self.__data_length = DLC
        self.__data = DATA

    def get_ID(self):
        return self.__ID

    def get_NODEID(self):
        return (self.__ID & 0x7F)

    def get_TYPE(self):
        return ((self.__ID >> 7) & 0x0F)

    def get_DATA(self):
        return self.__data

class Adapter:
    def __init__(self):
        self.__port = ''
        self.__is_plugged = False
        self.__buffer = list()

        self.__frame_state = 0
        self.__temp_frame_ID = 0
        self.__temp_frame_DLC = 0
        self.__temp_frame_DATA = list()
        self.__temp_frame_COMSTAT = 0
        self.__last_frame = None

        self.__adapter_frame = tk.Frame(window, bg="white")
        self.__adapter_label = tk.Label(self.__adapter_frame, bg="white", text="Adapter", anchor=tk.W, padx=20, font=("Arial Rounded MT Bold", 14))
        self.__port_papam_label = tk.Label(self.__adapter_frame, bg="white", text="Port", anchor=tk.W, padx=20) #font=("Arial Rounded MT Bold", 14))
        self.__port_text = tk.StringVar(self.__adapter_frame, "None")
        self.__port_label = tk.Label(self.__adapter_frame, bg="white", textvariable=self.__port_text, anchor=tk.W, padx=10)
        self.__send_button = tk.Button(self.__adapter_frame, bg="white", text="Send", command = self.send, anchor=tk.W, padx=10)
        self.__send_message = tk.StringVar(self.__adapter_frame, "None")
        self.__send_entry = tk.Entry(self.__adapter_frame, textvariable=self.__send_message)


        self.__adapter_frame.columnconfigure(0, minsize=150, weight=1)
        self.__adapter_frame.columnconfigure(1, minsize=150, weight=1)
        self.__adapter_label.grid(column=0, row=0, sticky=tk.EW, padx=5, pady=5) 
        self.__port_papam_label.grid(column=0, row=1, sticky=tk.EW, padx=5, pady=5)       
        self.__port_label.grid(column=1, row=1, sticky=tk.EW, padx=5, pady=5)
        self.__send_button.grid(column=0, row=2, sticky=tk.EW, padx=5, pady=5)
        self.__send_entry.grid(column=1, row=2, sticky=tk.EW, padx=5, pady=5)
        
    def is_plugged(self):
        if self.__port == '':
            while self.__port == '':
                for port in serial.tools.list_ports.comports():
                    if port.vid == 1240 and port.pid == 223:
                        self.__port = port
                        #self.__port_name = port.name
                window.update()
                time.sleep(0.1)
            self.ser = serial.Serial(self.__port.device, 230400, timeout=0, ) #non-blocking mode, return immediately in any case, returning zero or more, up to the requested number of bytes
            self.ser.close()
            self.ser.open()

        if self.__port in serial.tools.list_ports.comports():
            self.__port_text.set(self.__port.name)
            self.__is_plugged = True
        else:
            self.__is_plugged = False
            self.ser.close()
        return self.__is_plugged

    def process(self):
        try:
            self.__buffer.extend(self.ser.read(10000))
        except serial.SerialTimeoutException:
            pass
        except:
            self.__port = ''
            self.is_plugged()
            return None           
        if self.__frame_state == 0 :
            while len(self.__buffer) > 0 and self.__buffer[0] != 0x55:
                self.__buffer.pop(0)     
            if len(self.__buffer) > 1 and self.__buffer[0] == 0x55 and self.__buffer[1] == 0xAA:
                self.__buffer.pop(0)
                self.__buffer.pop(0)

                #Reset temp frame
                self.__temp_frame_ID = 0
                self.__temp_frame_DLC = 0
                self.__temp_frame_DATA.clear()
                self.__temp_frame_COMSTAT = 0
                self.__last_frame = None

                self.__frame_state = 1
        if self.__frame_state == 1 :
            if len(self.__buffer) > 1 :
                self.__temp_frame_ID = self.__buffer.pop(0)
                self.__temp_frame_ID = (self.__temp_frame_ID<<8) | (self.__buffer.pop(0))
                self.__frame_state = 2
        if self.__frame_state == 2 :
            if len(self.__buffer) > 0 :
                self.__temp_frame_DLC = (self.__buffer.pop(0) & 0x0F)
                self.__frame_state = 3
        if self.__frame_state == 3 :
            if len(self.__buffer) >= self.__temp_frame_DLC :
                for x in range(self.__temp_frame_DLC) :
                    self.__temp_frame_DATA.append(self.__buffer.pop(0))
                self.__frame_state = 4
        if self.__frame_state == 4 :
            if len(self.__buffer) > 0 :
                self.__temp_frame_COMSTAT = self.__buffer.pop(0)
                self.__frame_state = 0 
                self.__last_frame = CANFrame(self.__temp_frame_ID,self.__temp_frame_DLC,self.__temp_frame_DATA)
                return self.__last_frame
        return None           
    
    def send(self):
        string = [0x55, 0xAA]
        try:
            string+=bytearray.fromhex(self.__send_entry.get())
        except:
            tk.messagebox.showinfo("Error", "Incorrect format")
        else:
            #tk.messagebox.showinfo("Example", string)
            self.ser.write(string) #b'hello')
            self.__send_entry.delete(0, 'end')
        #msg=tk.messagebox.showinfo("Hello", "Hello")
        #return None

    def show_frame(self):
        self.__adapter_frame.pack(fill=tk.X)
        #self.__adapter_frame.pack_propagate(False) 
        #self.__port_label.pack(side = tk.LEFT)
        #self.__port_papam_label.pack(side = tk.RIGHT)

    def hide_frame(self):
        self.__adapter_frame.pack_forget()
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

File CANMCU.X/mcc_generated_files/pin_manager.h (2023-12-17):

/**
  @Generated Pin Manager Header File

  @Company:
    Microchip Technology Inc.

  @File Name:
    pin_manager.h

  @Summary:
    This is the Pin Manager file generated using PIC10 / PIC12 / PIC16 / PIC18 MCUs

  @Description
    This header file provides APIs for driver for .
    Generation Information :
        Product Revision  :  PIC10 / PIC12 / PIC16 / PIC18 MCUs - 1.81.7
        Device            :  PIC18F26K83
        Driver Version    :  2.11
    The generated drivers are tested against the following:
        Compiler          :  XC8 2.31 and above
        MPLAB 	          :  MPLAB X 5.45	
*/

/*
    (c) 2018 Microchip Technology Inc. and its subsidiaries. 
    
    Subject to your compliance with these terms, you may use Microchip software and any 
    derivatives exclusively with Microchip products. It is your responsibility to comply with third party 
    license terms applicable to your use of third party software (including open source software) that 
    may accompany Microchip software.
    
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
    IN NO EVENT WILL MICROCHIP BE LIABLE FOR ANY INDIRECT, SPECIAL, PUNITIVE, 
    INCIDENTAL OR CONSEQUENTIAL LOSS, DAMAGE, COST OR EXPENSE OF ANY KIND 
    WHATSOEVER RELATED TO THE SOFTWARE, HOWEVER CAUSED, EVEN IF MICROCHIP 
    HAS BEEN ADVISED OF THE POSSIBILITY OR THE DAMAGES ARE FORESEEABLE. TO 
    THE FULLEST EXTENT ALLOWED BY LAW, MICROCHIP'S TOTAL LIABILITY ON ALL 
    CLAIMS IN ANY WAY RELATED TO THIS SOFTWARE WILL NOT EXCEED THE AMOUNT 
    OF FEES, IF ANY, THAT YOU HAVE PAID DIRECTLY TO MICROCHIP FOR THIS 
    SOFTWARE.
*/

#ifndef PIN_MANAGER_H
#define PIN_MANAGER_H

/**
  Section: Included Files
*/

#include <xc.h>

#define INPUT   1
#define OUTPUT  0

#define HIGH    1
#define LOW     0

#define ANALOG      1
#define DIGITAL     0

#define PULL_UP_ENABLED      1
#define PULL_UP_DISABLED     0

// get/set RB0 procedures
#define RB0_SetHigh()            do { LATBbits.LATB0 = 1; } while(0)
#define RB0_SetLow()             do { LATBbits.LATB0 = 0; } while(0)
#define RB0_Toggle()             do { LATBbits.LATB0 = ~LATBbits.LATB0; } while(0)
#define RB0_GetValue()              PORTBbits.RB0
#define RB0_SetDigitalInput()    do { TRISBbits.TRISB0 = 1; } while(0)
#define RB0_SetDigitalOutput()   do { TRISBbits.TRISB0 = 0; } while(0)
#define RB0_SetPullup()             do { WPUBbits.WPUB0 = 1; } while(0)
#define RB0_ResetPullup()           do { WPUBbits.WPUB0 = 0; } while(0)
#define RB0_SetAnalogMode()         do { ANSELBbits.ANSELB0 = 1; } while(0)
#define RB0_SetDigitalMode()        do { ANSELBbits.ANSELB0 = 0; } while(0)

// get/set RB1 procedures
#define RB1_SetHigh()            do { LATBbits.LATB1 = 1; } while(0)
#define RB1_SetLow()             do { LATBbits.LATB1 = 0; } while(0)
#define RB1_Toggle()             do { LATBbits.LATB1 = ~LATBbits.LATB1; } while(0)
#define RB1_GetValue()              PORTBbits.RB1
#define RB1_SetDigitalInput()    do { TRISBbits.TRISB1 = 1; } while(0)
#define RB1_SetDigitalOutput()   do { TRISBbits.TRISB1 = 0; } while(0)
#define RB1_SetPullup()             do { WPUBbits.WPUB1 = 1; } while(0)
#define RB1_ResetPullup()           do { WPUBbits.WPUB1 = 0; } while(0)
#define RB1_SetAnalogMode()         do { ANSELBbits.ANSELB1 = 1; } while(0)
#define RB1_SetDigitalMode()        do { ANSELBbits.ANSELB1 = 0; } while(0)

// get/set RB2 procedures
#define RB2_SetHigh()            do { LATBbits.LATB2 = 1; } while(0)
#define RB2_SetLow()             do { LATBbits.LATB2 = 0; } while(0)
#define RB2_Toggle()             do { LATBbits.LATB2 = ~LATBbits.LATB2; } while(0)
#define RB2_GetValue()              PORTBbits.RB2
#define RB2_SetDigitalInput()    do { TRISBbits.TRISB2 = 1; } while(0)
#define RB2_SetDigitalOutput()   do { TRISBbits.TRISB2 = 0; } while(0)
#define RB2_SetPullup()             do { WPUBbits.WPUB2 = 1; } while(0)
#define RB2_ResetPullup()           do { WPUBbits.WPUB2 = 0; } while(0)
#define RB2_SetAnalogMode()         do { ANSELBbits.ANSELB2 = 1; } while(0)
#define RB2_SetDigitalMode()        do { ANSELBbits.ANSELB2 = 0; } while(0)

// get/set RB3 procedures
#define RB3_SetHigh()            do { LATBbits.LATB3 = 1; } while(0)
#define RB3_SetLow()             do { LATBbits.LATB3 = 0; } while(0)
#define RB3_Toggle()             do { LATBbits.LATB3 = ~LATBbits.LATB3; } while(0)
#define RB3_GetValue()              PORTBbits.RB3
#define RB3_SetDigitalInput()    do { TRISBbits.TRISB3 = 1; } while(0)
#define RB3_SetDigitalOutput()   do { TRISBbits.TRISB3 = 0; } while(0)
#define RB3_SetPullup()             do { WPUBbits.WPUB3 = 1; } while(0)
#define RB3_ResetPullup()           do { WPUBbits.WPUB3 = 0; } while(0)
#define RB3_SetAnalogMode()         do { ANSELBbits.ANSELB3 = 1; } while(0)
#define RB3_SetDigitalMode()        do { ANSELBbits.ANSELB3 = 0; } while(0)

// get/set IO_RB4 aliases
#define IO_RB4_TRIS                 TRISBbits.TRISB4
#define IO_RB4_LAT                  LATBbits.LATB4
#define IO_RB4_PORT                 PORTBbits.RB4
#define IO_RB4_WPU                  WPUBbits.WPUB4
#define IO_RB4_OD                   ODCONBbits.ODCB4
#define IO_RB4_ANS                  ANSELBbits.ANSELB4
#define IO_RB4_SetHigh()            do { LATBbits.LATB4 = 1; } while(0)
#define IO_RB4_SetLow()             do { LATBbits.LATB4 = 0; } while(0)
#define IO_RB4_Toggle()             do { LATBbits.LATB4 = ~LATBbits.LATB4; } while(0)
#define IO_RB4_GetValue()           PORTBbits.RB4
#define IO_RB4_SetDigitalInput()    do { TRISBbits.TRISB4 = 1; } while(0)
#define IO_RB4_SetDigitalOutput()   do { TRISBbits.TRISB4 = 0; } while(0)
#define IO_RB4_SetPullup()          do { WPUBbits.WPUB4 = 1; } while(0)
#define IO_RB4_ResetPullup()        do { WPUBbits.WPUB4 = 0; } while(0)
#define IO_RB4_SetPushPull()        do { ODCONBbits.ODCB4 = 0; } while(0)
#define IO_RB4_SetOpenDrain()       do { ODCONBbits.ODCB4 = 1; } while(0)
#define IO_RB4_SetAnalogMode()      do { ANSELBbits.ANSELB4 = 1; } while(0)
#define IO_RB4_SetDigitalMode()     do { ANSELBbits.ANSELB4 = 0; } while(0)

// get/set RC6 procedures
#define RC6_SetHigh()            do { LATCbits.LATC6 = 1; } while(0)
#define RC6_SetLow()             do { LATCbits.LATC6 = 0; } while(0)
#define RC6_Toggle()             do { LATCbits.LATC6 = ~LATCbits.LATC6; } while(0)
#define RC6_GetValue()              PORTCbits.RC6
#define RC6_SetDigitalInput()    do { TRISCbits.TRISC6 = 1; } while(0)
#define RC6_SetDigitalOutput()   do { TRISCbits.TRISC6 = 0; } while(0)
#define RC6_SetPullup()             do { WPUCbits.WPUC6 = 1; } while(0)
#define RC6_ResetPullup()           do { WPUCbits.WPUC6 = 0; } while(0)
#define RC6_SetAnalogMode()         do { ANSELCbits.ANSELC6 = 1; } while(0)
#define RC6_SetDigitalMode()        do { ANSELCbits.ANSELC6 = 0; } while(0)
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

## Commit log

2023-12-16 Initial HW upload
    [Test-B_Cu.gbr, Test-B_Mask.gbr, Test-B_SilkS.gbr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]
2023-12-17 Firmware added
    [Test-B_Cu.gbr, Test-B_Mask.gbr, Test-B_SilkS.gbr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]
2025-11-23 Added send button callback
2026-01-15 Fixed DLC value (trimmed to 4 bits)
    [CANCDC.py, main.c]
2026-01-16 CAN bus message injection function added
2026-01-17 Implemented interrupt-based uart
2026-01-17 Fixed CANCDC CAN operation mode
    [main.c]
2026-01-17 Switched both CANMCU and CANCDC projects to 125k baud rate
